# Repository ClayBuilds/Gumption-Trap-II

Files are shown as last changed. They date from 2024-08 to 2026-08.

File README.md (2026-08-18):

Gumption Trap II is an open source autonomous bathymetry robot.
This repository includes main code, CAD, data processing scripts, and other misc info.

Portfolio page links to more details and pictures about this build and its missions:

CNC routing a measured lakebed: https://www.clay-p-mcpherson.com/projects/cnc-routing-bathymetry-from-autonomous-boat/

Bathymetry survey demo: https://www.clay-p-mcpherson.com/projects/gumption-trap-ii-bathymetry-demonstration/

Original build: https://www.clay-p-mcpherson.com/projects/auto-solar-boat-v2-build/

These youtube videos are great resources for more in depth information:

See build and hardware explained here: https://youtu.be/iBlCVzS1J_o

Example depth plotting mission and operation: https://youtu.be/ZLng0cCmeMA

CNC routing bathymetry: https://youtu.be/M3wRNkO52RA

This project was created by me and only by me, Clay M. 
This project is entirely unaffiliated with any acadamic group, organization, business, etc. 
This project is exclusively a hobby, always has been, and always will be.
This project is not monetized or commercialized in any way, nor will it ever be.
Please do not attempt to contact me directly. I am not interested in any form of private collaboration.

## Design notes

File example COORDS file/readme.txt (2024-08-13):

keep the format the same as this COORDS.TXT example, but change the actual GPS latitude and longitude. The number in the first row is the number of coordinate pairs.

There is a variable in the arduino code that limits the maximum number of readable coordinates to save memory. Modify that number as necessary.

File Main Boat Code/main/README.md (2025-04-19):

All the files in this folder "main" are the entire arduino sketch intended to run on a Teensy 4.0
I recommend using the Arduino IDE for these, open the file "main.ino". All must be kept in a folder called "main".

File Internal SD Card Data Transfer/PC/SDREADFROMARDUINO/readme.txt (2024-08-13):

if it exists, delete the contents of the folder "sd_card_files" before use. Python script will copy all contents of the onboard SD card.

Close the arduino IDE after "SDREADTOPC" is uploaded. Power cycle the arduino, then run the python script.

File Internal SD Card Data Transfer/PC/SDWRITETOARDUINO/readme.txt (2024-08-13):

NOTE: WRITING TO ARDUINO WILL ERASE ALL EXISTING CONTENTS OF THE ONBOARD SD CARD. COPY DATA OFF OF IT BEFORE WRITING NEW DATA.

Place a "COORDS.TXT" file in the folder "filestosend". before use. Python script will copy all contents to the onboard SD card.

Close the arduino IDE after "SDWRITETOARDUINO" is uploaded. Power cycle the arduino, then run the python script.

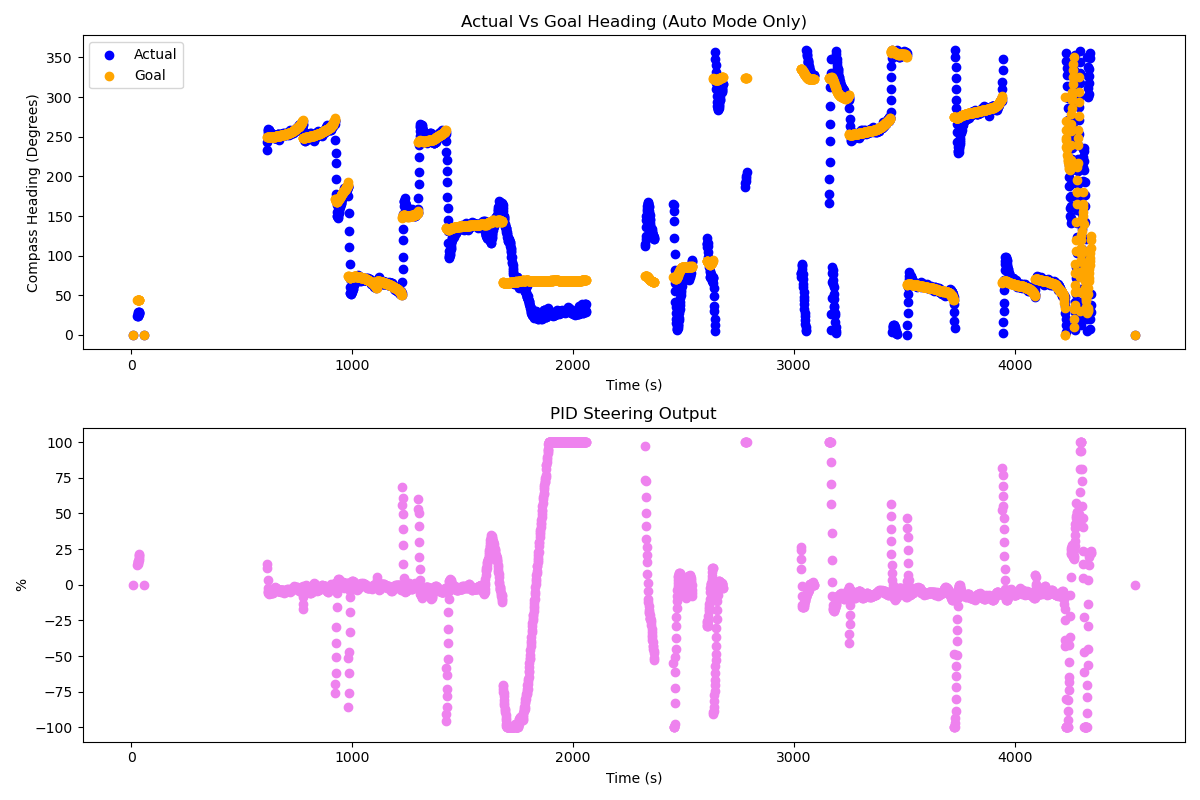
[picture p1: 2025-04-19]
Python Data Processing/Example Outputs/Figure_3.png

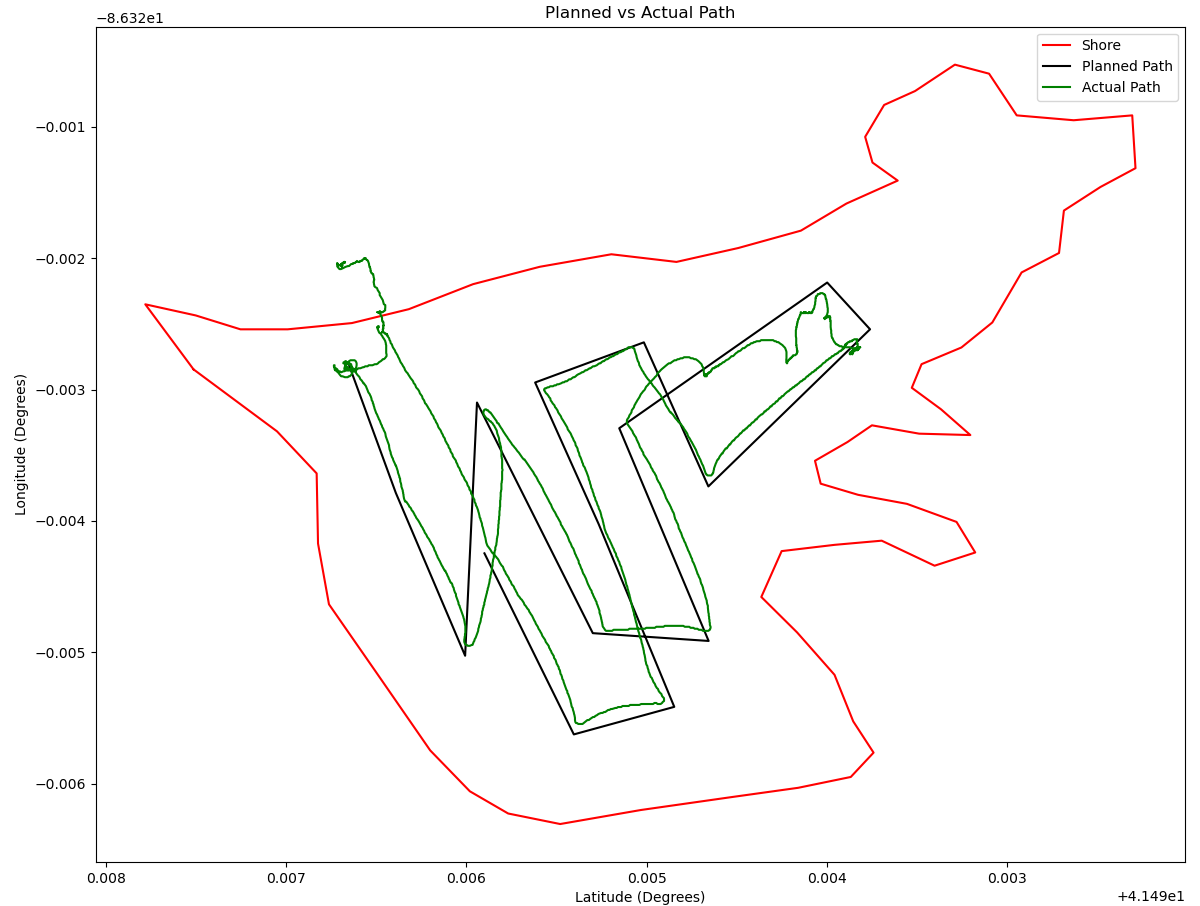
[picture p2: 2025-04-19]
Python Data Processing/Example Outputs/Figure_5.png

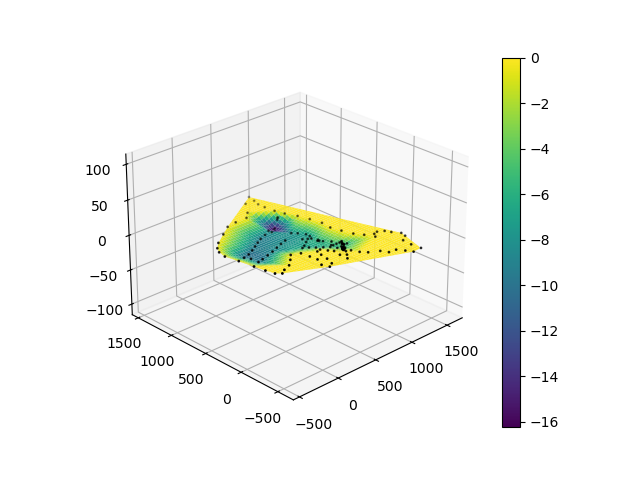
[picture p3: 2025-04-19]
Python Data Processing/Example Outputs/Figure_1.png

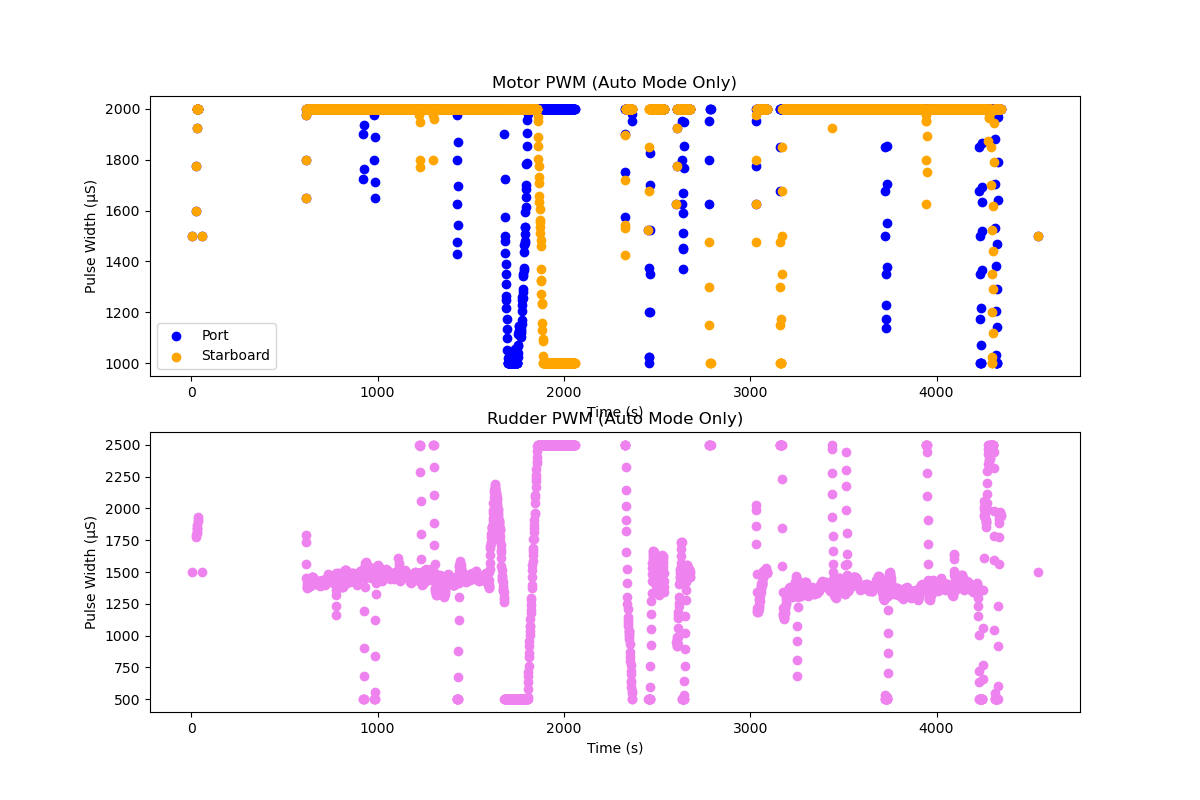
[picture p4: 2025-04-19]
Python Data Processing/Example Outputs/Figure_2.png

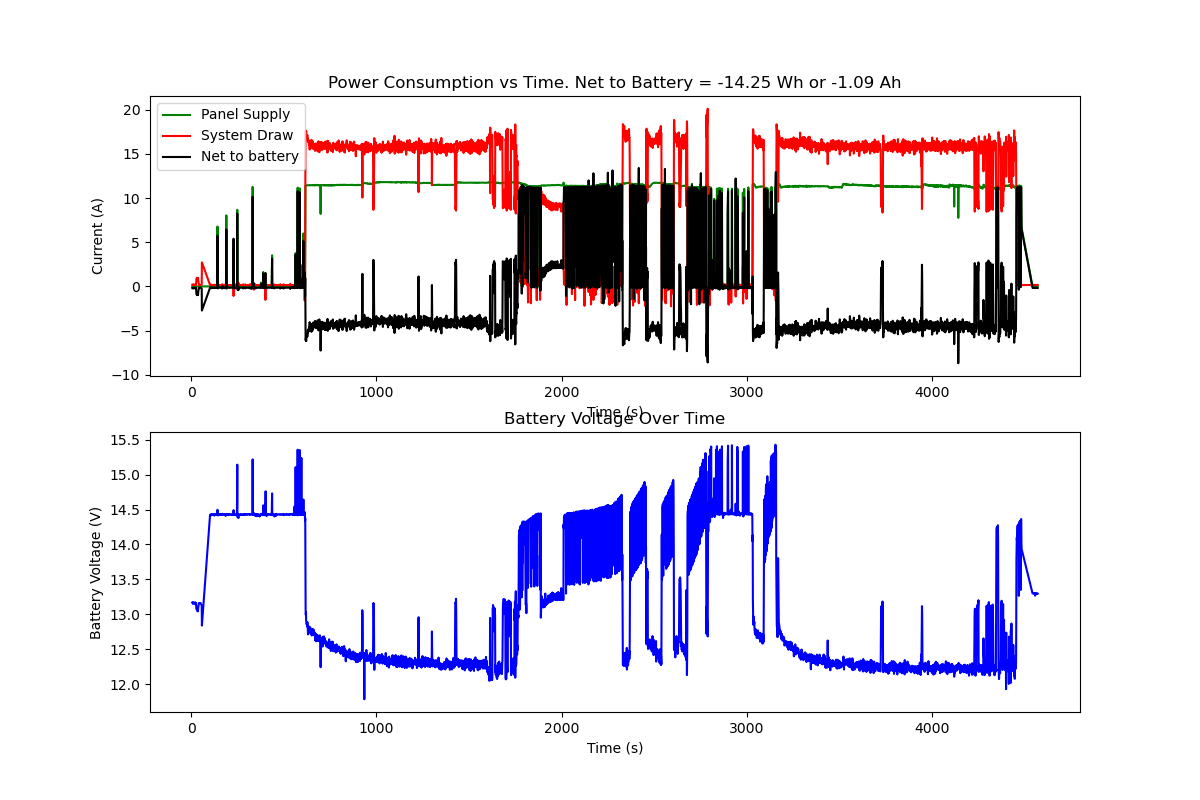
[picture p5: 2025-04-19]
Python Data Processing/Example Outputs/Figure_4.png

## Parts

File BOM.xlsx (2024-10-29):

GUMPTION TRAP 2.0 BOM
item | name | description | part no | source | qty | weight ea (lb) | weight total (lb) | cost ea | cost total | link | note
1 | 1/4-20 x 9" Hex Screw | largebolts that attach panel assemblies to deck mounts | 92800A368 | McMaster | 8 | 0.1 | 0.8 | 4.73 | 37.84 | https://www.mcmaster.com/92800A368/ | could save money with cheap threaded rods, but more difficult to assemble
2 | Short Bar Mount | 3d printed mount which captures nut for item 1, epoxied to deck |  | 3D printed | 8 | 0.1 | 0.8 |  | 0
3 | Long Bar Mount | 3d printed mount which holds item 1, epoxied to deck |  | 3D printed | 8 | 0.2 | 1.6 |  | 0
4 | rudder | laser cut acryllic |  | DIY laser | 1 |  |  |  | 0
5 | battery | 12v 10Ah LiFePO4 with BMS | ECO-LFP1210 | ebay | 2 | 2.3 | 4.6 |  | 0
6 | Rudder Servo | dfrobot 45kg ip67 servo | d5545gs | digikey | 1 | 0.2 | 0.2 |  | 0 | https://www.hobbyporter.com/products/e-power-d5545gs-aluminum-case-metal-grear-coreless-digital-45kg-011sec-hv-servo-3556 | range 500-1500-2500 us
7 | 10-32 ball joint rod end | one right hand, one left hand | 60645K11 (https://www.mcmaster.com/catalog/60645K11) | McMaster | 2 |  | 0 | 4.4 | 8.8 | https://www.mcmaster.com/catalog/130/1481/60645K11
8 | 10-32 turnbuckle coupler | to be cut in half to form tie rod threaded ends | 8419K126 (https://www.mcmaster.com/catalog/8419K126) | McMaster | 1 |  | 0 | 10.7 | 10.7 | https://www.mcmaster.com/catalog/130/1488/8419K126
9 | Complete Hull Assembly stbd | painted hull with deck, deck fasteners, gasket, etc. |  | Homebuilt | 1 | 15.2 | 15.2
10 | Complete Hull Assembly port | painted hull with deck, deck fasteners, gasket, etc. |  | Homebuilt | 1 | 17.7 | 17.7 |  |  |  | This hull was made first and less well built with excess epoxy and fiberglass
11 | Large rudder pulley | 60 tooth gt2 pulley |  | Amazon | 1 | 0.1 | 0.1 | 4.5 |  | https://www.amazon.com/gp/product/B09JSQ1W3S/ref=ppx_yo_dt_b_asin_title_o06_s00?ie=UTF8&th=1
12 | Small Rudder pulley | 32 tooth gt2 pulley |  | 3D printed | 1 |  | 0 |  |  |  | model based on McMaster 3764N112
13 | Belt | gt2 belt, 200mm length |  | unknown | 1 |  | 0
14 | Solar Panel | Harbor Freight 100W 18VDC nominal | 57325 | Harbor Freight | 2 | 15 | 30 |  |  | https://www.harborfreight.com/100-watt-monocrystalline-solar-panel-57325.html
15 | battery mount | holds batteries inside hulls |  | 3D printed | 4 |  | 0
16 | motor mount bracket | sheet metal aluminium, holds motors and rudders to hulls |  | send cut send | 2 | 0.3 | 0.6 |  |  |  | sheet metal bending, I had a mistake in my model for the motor hole pattern, check CAD before reordering
17 | motor | Chinese no name, generic submersible 3 phase BLDC, ~300kv | VGEBY1 F2838-350KV | Amazon | 2 |  | 0
18 | propellor | torroidal, resin printed |  | 3D printed | 2 |  | 0
19 | ping echosounder | ping2 |  | blue robotics | 1 | 0.4 | 0.4 | 410
20 | ping shroud |  |  | 3D printed | 1 |  | 0
21 | upper rudder bracket | holds rudder to upper mount |  | 3D printed | 2 |  | 0
22 | lower rudder bracket | holds rudder to lower mount |  | 3D printed | 2 |  | 0
23 | transom plate | 1/4" 316ss with 1/4-20 mounting holes |  | commercial laser | 2 | included in hull
24 | motor mount bracket spacers | various sizes, adjusted to straighten the mounts |  | 3D printed | 4 |  | 0
25 | motor mount bracket bolts | 1/4-20, various lengths |  | Local Hardware | 8 | 0.01 | 0.08
26 | pcbmount | holds pcb inside hull |  | 3D printed | 1 | 0.17
27 | ESC | bidirectional, 50A 3 phase BLDC |  | Amazon | 2
28 | 3 pin bulkheads |  |  | digikey
29 | 3 pin plugs |  |  | digikey
30 | 10 pin plug | plug, female, 10p, solder cup | 2150-22010211-01-ND | digikey | 1
31 | 10 pin bulkhead | receptacle, male, 10pos, solder cup | 2150-22010515-01-ND | digikey | 1
32 | solar charge controller | 12v 100A Chinese | X003BAPJCB 23EB0028 A3D472F |  | 1 | 0.61
33 | charge controller mount | holds solar charge controller inside hull |  | 3D printed | 1 | 0.17
34 | main PCB | custom, gumption trap version 1.2 |  | JLCPCB |  | 0.22 |  |  |  |  | weight as assembled including all electronics, mount, hardware, antenna adapter
35 | current sensor | INA260 |  | adafruit | 2
36 | gps module | NEO-6M |  |  | 1
37 | remote gps antenna |  |  | adafruit | 1
38 | remote gps antenna adapter |  |  | adafruit | 1
39 | magnetometer |  | LSM303AGR | adafruit | 1
40 | i2c breakout board |  |  | adafruit | 1
41 | sd card reader |  | Adafruit Micro-SD Breakout Board+ (PID 264) | adafruit | 1
42 | teensy 4.0 |  |  | Microcenter | 1
43 | 3v3 regulator |  |  |  | 2 |  |  |  |  |  | on PCB, supplies components that need 3v
44 | capacitor |  |  |  | 2 |  |  |  |  |  | on PCB, for smoothing power
45 | DC DC converter | 5A, Buck/Boost | DFR0946 | Dfrobot | 1 | 0.15 |  | 8.9
46 | Aluminum Extrusions | 2020 profile, used as framework for hull to panel attachment |  | ebay
47 | Servo Mount | PETG for high strength and UV resistance. |  | 3D printed | 1
48 | Servo Linkage | M3 RC Car tie rod with ball joints, no name brand |  | Hobbytown USA | 2
49 | lower strut mount | resin printed, easily removeable fit |  | 3D printed | 1 | 0.5
50 | Upper Strut Mount | FDM printed, white for less sun absoption. Mounts receivers |  | 3D printed | 1 | 0.15
51 | Strut | Aluminium aero profile, 3/4" streamline | Stock # 1105 | KS Precision Metals | 1
52 | 10-32 left hand nut | for tie rod |  | McMaster | 1
53 | tie rod | aluminium tube, JB welded to turnbuckle coupler halves |  | Home Depot | 1
54 | RC Receiver | Flysky FS-iA6B | Flysky FS-iA6B |  | 1
55 | RC Transmitter | Handheld | Flysky FS-i6X
56 | Shoulder Screw | used as half axle for rudder | 94035A309 | McMaster | 4 |  |  | 6.67
56 | Nylon Sleeve Bearing | bushing for rudder | 6389K445 | McMaster | 4 |  |  | 0.94

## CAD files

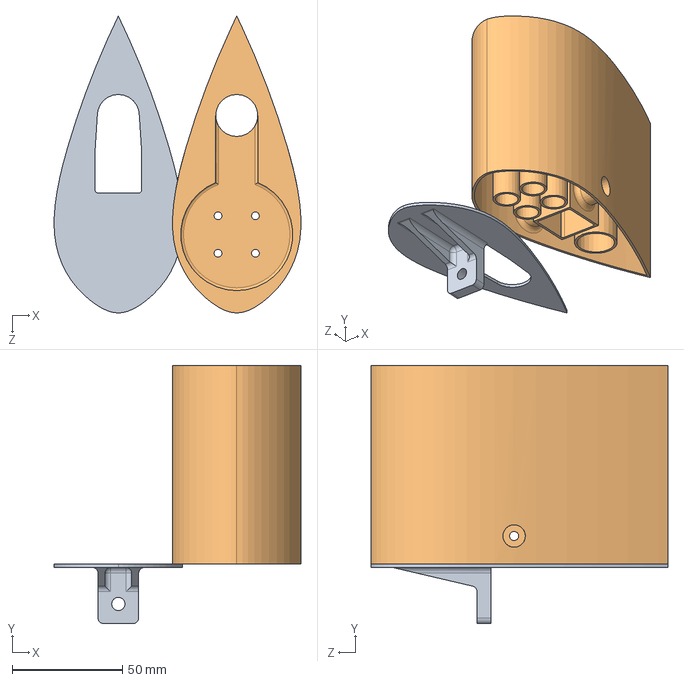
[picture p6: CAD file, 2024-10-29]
CAD/ping2subassy.SLDASM
111.9 x 117.0 x 134.6 mm
ping2shroud
ping

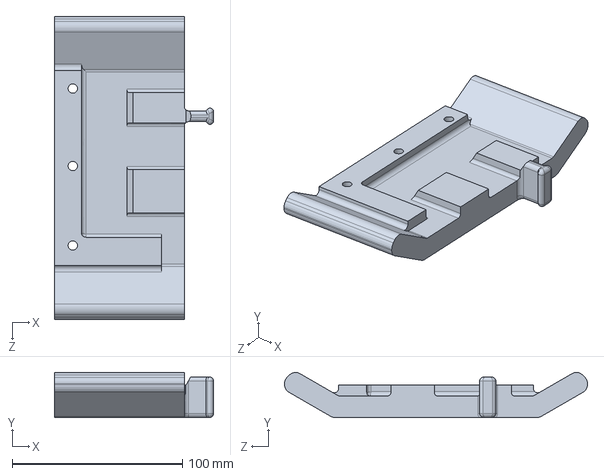
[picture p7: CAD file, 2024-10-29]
CAD/pcbmount.SLDPRT
93.4 x 26.5 x 177.8 mm

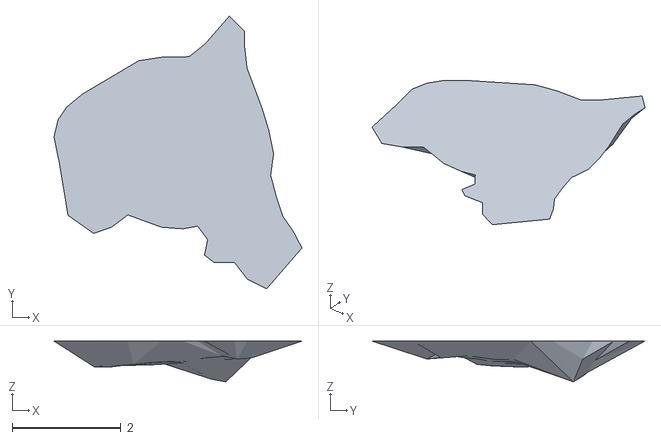
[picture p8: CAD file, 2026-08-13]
Python Data Processing/3D Model Generation/output/output.stl
4.56 x 5.02 x 0.75

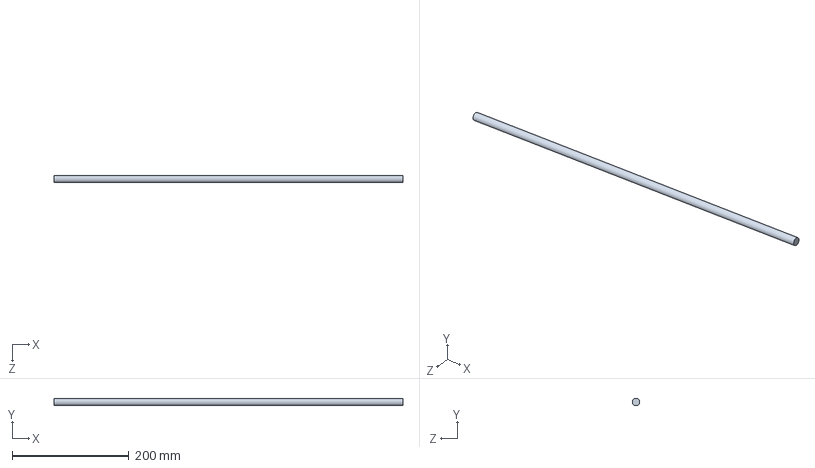
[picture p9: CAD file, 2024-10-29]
CAD/tie rod.SLDPRT
596.9 x 12.7 x 12.7 mm

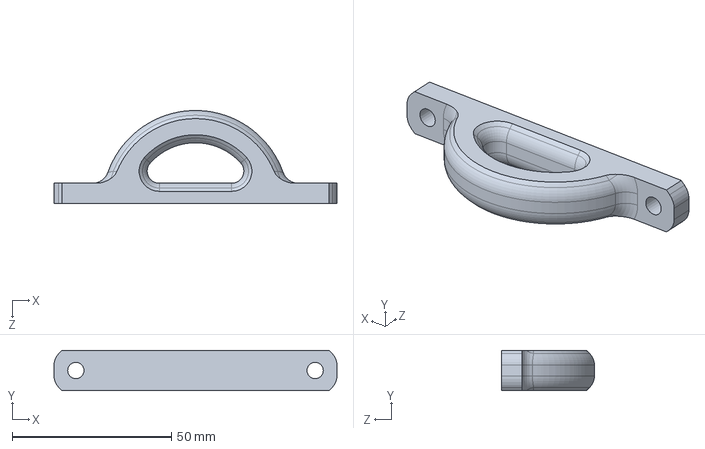
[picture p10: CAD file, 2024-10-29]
CAD/cleet.SLDPRT
88.9 x 12.7 x 29.2 mm

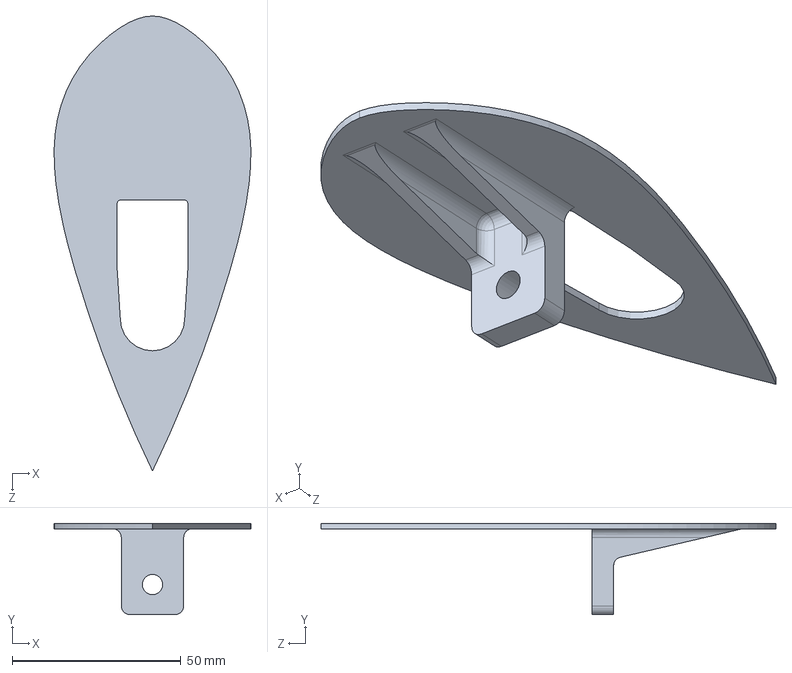
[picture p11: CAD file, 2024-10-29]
CAD/ping.SLDPRT
58.2 x 27.0 x 134.6 mm

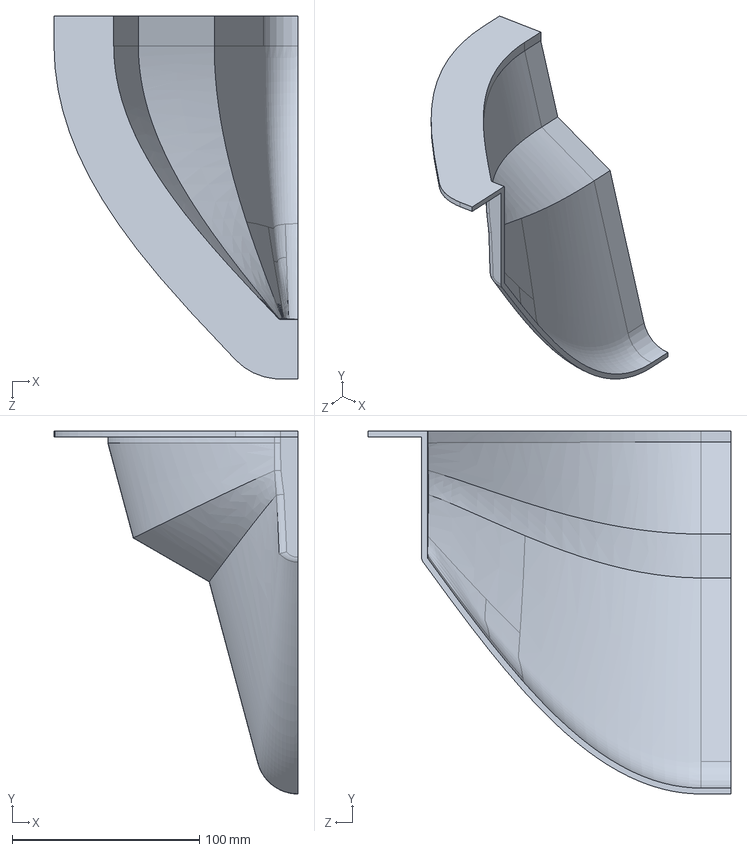
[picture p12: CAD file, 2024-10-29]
CAD/pontoon.SLDPRT
130.2 x 193.7 x 193.7 mm

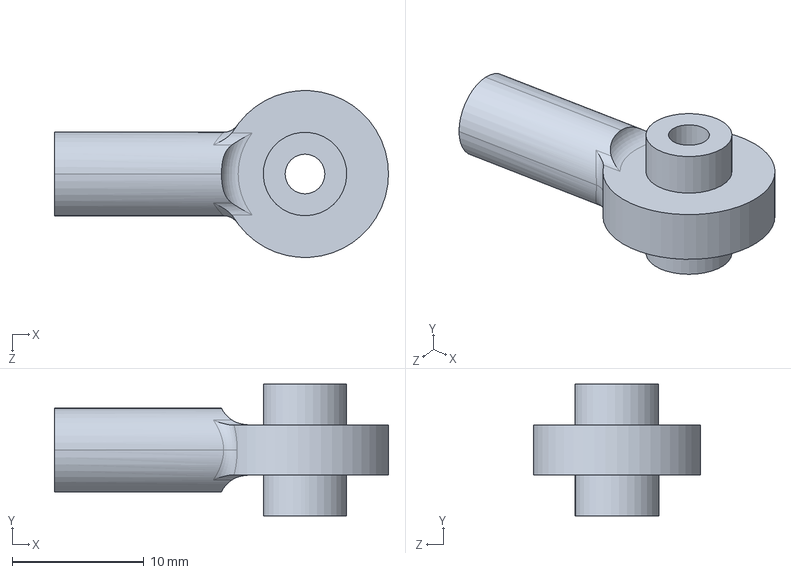
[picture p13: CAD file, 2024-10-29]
CAD/servo linkage ball joint.SLDPRT
25.4 x 10.0 x 12.7 mm

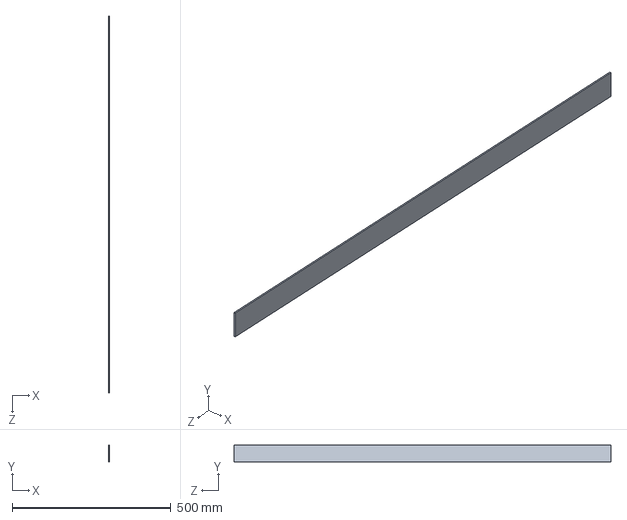
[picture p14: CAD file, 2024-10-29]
CAD/flat mold panel.SLDPRT
3.17 x 53.3 x 1188.5 mm

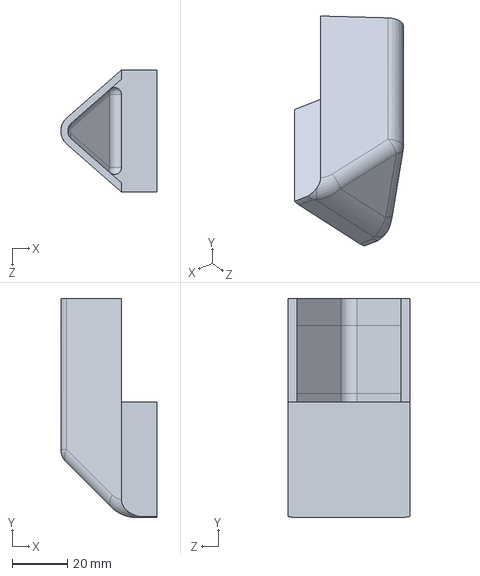
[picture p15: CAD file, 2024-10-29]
CAD/motor mount fairing.SLDPRT
35.0 x 79.6 x 44.5 mm

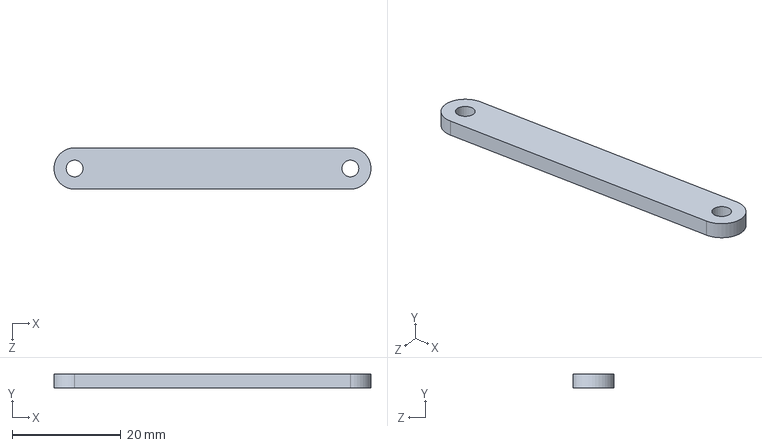
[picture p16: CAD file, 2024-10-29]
CAD/reference servo link.SLDPRT
58.4 x 2.54 x 7.62 mm

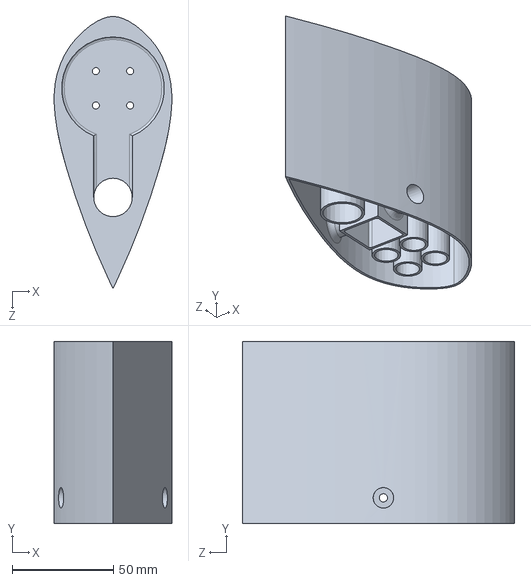
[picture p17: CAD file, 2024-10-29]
CAD/ping2shroud.SLDPRT
58.1 x 90.0 x 134.6 mm

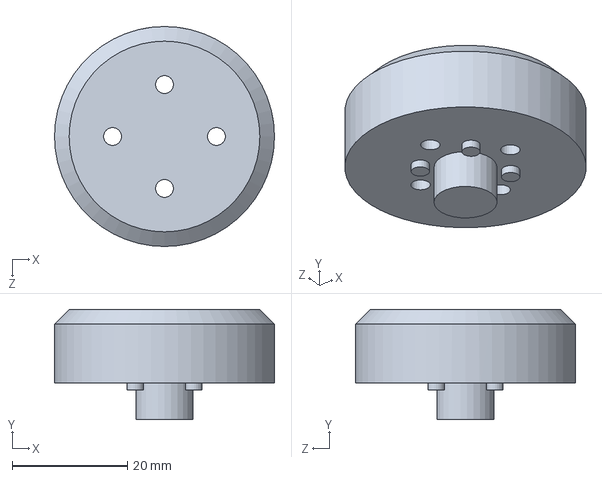
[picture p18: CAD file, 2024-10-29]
CAD/motor pattern drill guide.SLDPRT
38.1 x 19.0 x 38.1 mm

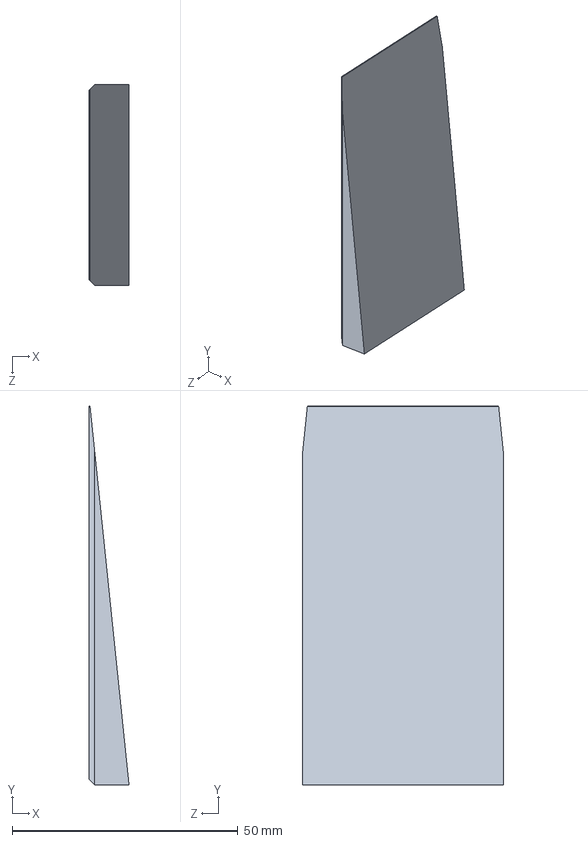
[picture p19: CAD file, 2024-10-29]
CAD/transom shim 1.SLDPRT
8.89 x 84.0 x 44.5 mm

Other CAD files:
CAD/Mold Assy.SLDASM
CAD/Main Assy.SLDASM
CAD/battery bracket.SLDPRT
CAD/servo mount 2.SLDPRT
CAD/2020 ext.SLDPRT
CAD/60645K111_Ball Joint Rod End.SLDPRT
CAD/6389K445_Light Duty Dry-Running Nylon Sleeve Bearing.SLDPRT
CAD/90975A071_Steel Tee Nut Inserts.SLDPRT
CAD/92196A571_18-8 Stainless Steel Socket Head Screw.SLDPRT
CAD/92800A368_18-8 Stainless Steel Hex Head Screw.SLDPRT
CAD/94035A309_18-8 Stainless Steel Precision Shoulder Screw.SLDPRT
CAD/98704A625_Plastic-Head Thumb Screw with Hex Drive.SLDPRT
CAD/99117A910_Steel Pan Head Phillips Screws.SLDPRT
CAD/BR-100725_RevA_PUBLIC.SLDPRT
CAD/Panel.SLDPRT
CAD/U Bolt Flat Bottom.SLDPRT
CAD/battery.SLDPRT
CAD/compassmount.SLDPRT
CAD/keel support.SLDPRT
CAD/large rudder pulley.SLDPRT
CAD/linkage version servo mount.SLDPRT
CAD/long bar mount.SLDPRT
CAD/lower motor bracket spacer.SLDPRT
CAD/lower rudder bracket.SLDPRT
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

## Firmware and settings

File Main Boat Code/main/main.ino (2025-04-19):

//Clay M
//Updated 4-19-2025

//GUMPTION TRAP II MAIN CODE
//This code written for custom PCB v1.2
//First version with newly rebuilt boat, Gumption Trap II. New hardware includes bidirectional ESCs and a rudder servo
//Designed to run on Gumption Trap II, a solar powered USV with two bidirectional brushless motors and a servo driven rudder system.
//Hardware also includes a GPS module, Magnetometer, Blue Robotics Ping Echo Sounder, two INA260 Current/Voltage Sensors and an SD card module.
//Main microcontroller is a PJRC Teensy 4.0

//Local Backup Version 3.11

//Changes from previous public upload (local backup 3.8):
/*
  -Improve PID tuning
  -now print serial debugging values only if USB plugged into laptop. Will run faster when unplugged this way.
  -other minor changes to make code run faster
*/

//Test Results: 
/*
  -Worked flawlessly in real world lake test. (4.12.25). Made sharp turns nicely without overshooting. 
  -Power consumption/generation was about 1:1 on a sunny day.
*/

#include <TinyGPSPlus.h>
#include <SoftwareSerial.h>
#include <SD.h>
#include <SPI.h>
#include <Adafruit_LIS2MDL.h>       
#include <Servo.h>
#include <Adafruit_INA260.h>
#include <ping1d.h>
#include <QuickPID.h>

#include "pindefinitions.h"
#include "miscfuncs.h"
#include "constvars.h"
#include "manualmode.h"
#include "automode.h"
#include "powersense.h"
#include "cardlogger.h"
#include "depthping.h"
#include "navigation.h"




void setup() 
{
  Serial.begin(115200);
  
  //make sure SD card is good
  if(!SD.begin(cs))
  {
    cardfailed = true;
    Serial.println("couldn't initialize");
  }
  else
  {
    cardfailed = false;
    Serial.println("SD Card Initialized");
  }

  if(!SD.exists("COORDS.txt"))
  {
    cardfailed = true;
    Serial.println("File Missing");
  }

  //pull coords off SD Card
  if(!cardfailed)
  {
    readcard();
    printCoords();
  }
  else
  {
    Serial.println(F("Card read failed"));
  }

  //check for magnetometer error
  if(!mag.begin())              
  {
    magerr = true;
    Serial.println("MAG ERROR");
    logerror(4);
  } 
  
  //setup ping sounder 
  Serial2.begin(115200);
  if(!ping.initialize())
  {
    Serial.println("PING ERROR");
    logerror(5);
  }
  
  //initialize gps serial connection
  Serial1.begin(9600);
  
  //drive control setup
  pinMode(throt, INPUT);
  pinMode(steer, INPUT);
  pinMode(swt, INPUT);

  //initialize motors
  port.attach(pmot,pwmlow,pwmhigh);
  starboard.attach(smot,pwmlow,pwmhigh);
  rudder.attach(rud,servlow,servhigh);

  port.write(pwmmid);          //set throttles to neutral to make sure ESC's will start up.
  starboard.write(pwmmid);
  rudder.write(servmid);
  portval = pwmmid;
  starbval = pwmmid;
  rudval = servmid;
  
  //setup power measurement chips (INA260)
  motpow.begin(0x41);   //note: one module needs a solder jumper so that they have different I2C addresses
  solpow.begin(0x40);
  
  //setup PID Control loop
  Setpoint = 0;
  steerPID.SetTunings(Kp, Ki, Kd);
  steerPID.SetOutputLimits(-100,100);
  steerPID.SetMode(0); //start in manual mode
  
  smartDelay(5000); //take some time to read gps data
  Serial.println("setup over");
}

void loop() 
{
  switchval = readSwitch(swt, false);  //check the mode toggle switch. if out of radio range, default to auto
  powersense();
  depthping();
  if(Serial)          //if usb is plugged in, print the debugging values
    {printvals();}
  blackboxwrite();
  pingwrite();
  navigate();
  steerPID.Compute();
  looptimecheck();
  
  if(!switchval)  //this extra if statement is a little redundant, included because I had plans for some other ways autostate might be enabled or disabled besides just switchval.
    {autostate = true;}
  else    
    {autostate = false;}  
    
  if(autostate)    
    {
      steerPID.SetMode(1); //automatic mode
      automode();
    }
  else
    {
      steerPID.SetMode(0); //manual mode
      manualmode();
    } 
}

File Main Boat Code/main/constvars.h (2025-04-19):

//This file for constant variables or parameters used across multiple areas of the code or for configuration purposes

#include "pindefinitions.h"
#include <SoftwareSerial.h>
#include <TinyGPSPlus.h>
#include <Adafruit_LIS2MDL.h>
#include <Adafruit_INA260.h>
#include <ping1d.h>

#ifndef CONST_VARS_h
#define CONST_VARS_h



const float Pi = 3.15159;


//SD card stuff
File coords;
File blackbox;
File depthlog;
File errorlog;
int bblast = 0;       //millis() of previous black box recording
int bbint = 1;       //seconds between black box recordings
int depthlast = 0;      //millis() of previous depth recording
int depthint = 30;      //seconds between depth measurements
bool cardfailed;
char cardcontents[25];
int cardsize;
byte i = 0;           //indexes for nested loops that read coordinate arrays
byte j = 0;
byte k = 1;
byte n;
const byte maxcoords = 25;    //maximum allowable number of gps coordinate pairs in mission. Helps save RAM

//GPS and auto navigation stuff
TinyGPSPlus gps;
float currentLat;               //present lattitude
float currentLong;              //present longitude
float goalLat = 39.03385;
float goalLong = 125.75432;
float Carray [2][maxcoords];        //array of latitude and longitude pairs (row 0 lat row 1 long, column 0 only contains the length)
byte ncoords = maxcoords;                         //number of coordinate pairs
double goalheading;
double hdiff;                   //difference between actual heading and goal heading
double hdarr[5] = {0};          //array of the last 5 hdiff values
double hdsum = 0;
double hdavg = 0;               //average of the last 5 hdiff values. This intended to smooth out jumpy magnetometer data.
byte waypoint = 1;
double d = 100;                 //distance to waypoint. Don't initalize as = 0
bool killhumansmode = false;

//Drive control stuff
Servo port;
Servo starboard;
Servo rudder;
int portval;        // actual pwm values in microseconds to feed ESCs
int starbval;
int rudval;
int goalport;       //goal pwm values for gradual adjustment
int goalstarb;    
int goalrud;
int switchval = 0;  //1 switch flipped 0 switch not flipped. 1 is manual control mode.
bool autostate = true;
int throtval = 0;   //throttle value. zero is dead stop, -100 is full power backwards, 100 is full power forwards
int steerval = 0;   //steering value. -100 is hard left, positive 100 is hard right, zero straight 
const float pwmhigh = 2000;   //pwm range values for installed ESCs. virtually always 1000-2000 for typical RC or drone parts. 
const float pwmmid = 1500;    //pwm midpoint for ESC neutral/startup
const float pwmlow = 1000;
const float servlow = 500;       //min, middle, max signals for full range of rudder servo
const float servmid = 1500;
const float servhigh = 2500;
const int pwmim = 100;         //milliseconds between each pwm adjustment for motor ESCs
const int pwmir = 100;          //milliseconds between each pwm adjustment for rudder servo; (NOTE: Rudder incremental adjustment not currenlty implemented)
const int pwmratem = 25;      //maximum allowed microseconds of pwm adjustment for motor ESCs per pwmim miliseconds. for example, a value of 1 and i of 10 would take 10 seconds to go from a pwm of 1000us to 2000us. a value of 5 would take 2 seconds.
const int pwmrater = 100;     //maximum allowed microseconds of pwm adjustment for rudder servo per pwmir miliseconds. for example, a value of 1 and i of 5 would take 10 seconds to go from a pwm of 500us to 2500us. a value of 5 would take 2 seconds.
unsigned long tlastp = 0;     //time in ms since last pwm adjustment
unsigned long tlasts = 0;
unsigned long tlastr = 0;

//PID Control
const float Kp = 0.75;     //proportional gain
const float Ki = .0625;    //integral gain
const float Kd = 0;        //derivative gain
float Setpoint, PIDInput, PIDOutput;
QuickPID steerPID(&PIDInput, &PIDOutput, &Setpoint);


//Magnetometer stuff
Adafruit_LIS2MDL mag = Adafruit_LIS2MDL(12345); 
bool magerr;                    //variable to tell if something went wrong with reading compass
float currentheading;
const float xoff = -19.87;        //from magnetometer calibration
const float yoff = -21.22;
const float declination = 3.1;    //from central texas 2024

//Power measurement stuff (INA260)
Adafruit_INA260 motpow = Adafruit_INA260(); //motor and whole system power consumption
Adafruit_INA260 solpow = Adafruit_INA260(); //solar power production
double motI = 0;  //mA
double solI = 0;
double motV = 0;  //mV
double solV = 0;
const double motIlimit = 20000; //mA at which forced throttle down should occur

//depth sounder stuff
Ping1D ping { Serial2 };
int depth = 0;

//error code stuff
int laste2 = 0;
int laste3 = 0;
int laste6 = 0;
int laste7 = 0;
int lastgoodhead = 0;

//for checking speed that program runs
unsigned long loopt = 0;
unsigned long looptlast = 0;

#endif

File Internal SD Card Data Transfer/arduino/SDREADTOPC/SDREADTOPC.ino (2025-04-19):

//SDREADTOPC
//Version 2, 7.3.24
//This code will copy everything from the connected SD card and spit it out to a python script running on a PC

//local backup v2
//changes from v1:
/*
-write ESCs to the neutral position
*/

#include <SPI.h>
#include <SD.h>
#include <Servo.h>

Servo port;
Servo starboard;

int pwmlow = 1000;
int pwmhigh = 2000;

const byte pmot = 4;
const byte smot = 3;

const int cs = 10; // chip select pin for SD card


void setup() 
{
  port.attach(pmot,pwmlow,pwmhigh);
  starboard.attach(smot,pwmlow,pwmhigh);

  port.write(1500);
  starboard.write(1500);

  Serial.begin(9600);
  while (!Serial) {
    ; // Wait for the serial port to connect. 
  }

  if (!SD.begin(cs)) {
    Serial.println("Initialization failed!");
    return;
  }
  Serial.println("Initialization done.");

  // List all files in the root directory
  File root = SD.open("/");
  printDirectory(root, 0);
  root.close();
}

void loop() {
  // Do nothing in the loop
}

void printDirectory(File dir, int numTabs) {
  while (true) {
    File entry = dir.openNextFile();
    if (!entry) {
      // No more files
      break;
    }
    for (uint8_t i = 0; i < numTabs; i++) {
      Serial.print('\t');
    }
    Serial.print(entry.name());
    if (entry.isDirectory()) {
      Serial.println("/");
      printDirectory(entry, numTabs + 1);
    } else {
      // Files have sizes, directories do not
      Serial.print("\t\t");
      Serial.println(entry.size(), DEC);
      if (String(entry.name()).endsWith(".TXT") || String(entry.name()).endsWith(".txt")) 
      {
        // Read and send the file content
        sendFileContent(entry.name());
      }
    }
    entry.close();
  }
}

void sendFileContent(const char *filename) {
  File file = SD.open(filename);
  if (file) {
    Serial.println(String("Start:") + filename);
    while (file.available()) {
      char buffer[64];
      int bytesRead = file.readBytes(buffer, sizeof(buffer));
      Serial.write(buffer, bytesRead);
      delay(10); // Adding a small delay to avoid overflow
    }
    Serial.println(String("End:") + filename);
    file.close();
  } else {
    Serial.println("Error opening " + String(filename));
  }
}

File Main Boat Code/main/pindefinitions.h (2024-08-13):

//This file includes all necessary pin definitions as wired on pcb 
//note: LED_BUILTIN can't be used cause pin 13 is SCK

#ifndef PIN_DEFINITIONS_h
#define PIN_DEFINITIONS_h

const byte gpsrx = 1;   //don't think I actually need rx/tx since I'm not using software serial anymore. These are the serial pins for the GPS module
const byte gpstx = 0;
const byte smot = 3;    //starboard motor PWM signal to ESC
const byte pmot = 4;    //port motor PWM signal to ESC
const byte rud = 14;    //PWM signal to rudder servo
const byte throt = 20;  //Throttle PWM signal coming from radio receiver in manual mode
const byte steer = 16;  //Steering PWM signal coming from radio receiver in manual mode
const byte swt = 17;    //auxiliary switch signal coming from radio receiver. toggles between auto/manual modes.
const byte cs = 10;     //chip select for SD card
const byte mosi = 11;   // other SPI pins 
const byte miso = 12;
const byte sck = 13;
const byte ping_arduinorx = 7; //don't think I actually need rx/tx since I'm not using software serial anymore. These are serial pins for the sonar module. 
const byte ping_arduinotx = 8;

#endif

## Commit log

2024-10-29 add rewritten mission data processing scripts
    includes depth plots, boat movement path plots, and black box data plots (power consumption, pwm output, etc.)
2024-10-29 add folder for CAD
    folder currently empty
2024-10-29 add CAD models for boat
    includes all CAD files for the entire project. All solidworks. Hull mold files are configurations inside the main pontoon geometry. Main assembly is titled "Main Assy". Consider Main Assy to be the m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
    [2020 ext.SLDPRT, 60645K111_Ball Joint Rod End.SLDPRT, 6389K445_Light Duty Dry-Running Nylon Sleeve Bearing.SLDPRT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]
2024-10-29 add BOM
    this BOM is incomplete and useful as a reference but not entirely representative of everything used in this project.
    [BOM.ods]
2024-10-29 add BOM in excel format
    it's the same as the .ods
    [BOM.xlsx]
2025-04-19 Minor updates and put in folder "main"
    Some minor code updates to PID tuning and speed improvements. All the arduino files are now in a folder called "main" so it matches the name of "main.ino" and the code can more easily be downloaded a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
2025-04-19 Delete Main Boat Code/powersense.h
    this file got updated and moved to Main Boat Code/main
2025-04-19 Delete Internal SD Card Data Transfer/arduino/SDREADTOPC/SDREADTOPC.v2 directory
    this file updated and local backup version# removed from name. redundant folder removed.
2025-04-19 Delete Internal SD Card Data Transfer/arduino/SDWRITEFROMPC/SDWRITEFROMPC.v2 directory
    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
